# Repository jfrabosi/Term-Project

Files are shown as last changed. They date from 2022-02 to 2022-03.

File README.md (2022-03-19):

# Project Proposal
The project our team is planning on developing is a pancake plotter. This system uses a 2.5 axis CNC system to interpret code and plot the batter on a griddle. 
The batter is contained in a 500 mL syringe which is moved along a radial arm via a motor belt system. The raidial arm is mounted to a second motor
which can rotate from -90 to 90 degrees. To reduce the amount of stress on the second motor, a semi-circle will be used to support the end of the radial 
arm. We plan to fabricate the entire system by using 80/20 1" tubing as the structure, using a gridle as a bed, using 3D-printed parts as mounts, and
using laser-cut plywood for the semi-circular support. A bill of materials, breaking down cost, as well as sketches and a gif of our system design can be seen in the figures below.

| Qty. | Part | Source | Est. Cost |
|:----:|:---|:---|:---:|
|  3 | Pittperson Gearmotors | ME405 Tub | - |
|  1 | Nucleo with Shoe | ME405 Tub | - |
|  1 | 500 mL Syringe | Amazon | $15.99  |
|  1 | Griddle | Amazon | $26.94  |
|  3 | 80/20 1" Tubing | Amazon | $14.54  |
|  1 | Spool PLA Plastic | Team's Supply | - |
|  1 | Sheet of Plywood | Amazon | $24.00  |
|  3 | Motor Driver | ME 405 Tub and Pololu | $4.95 |

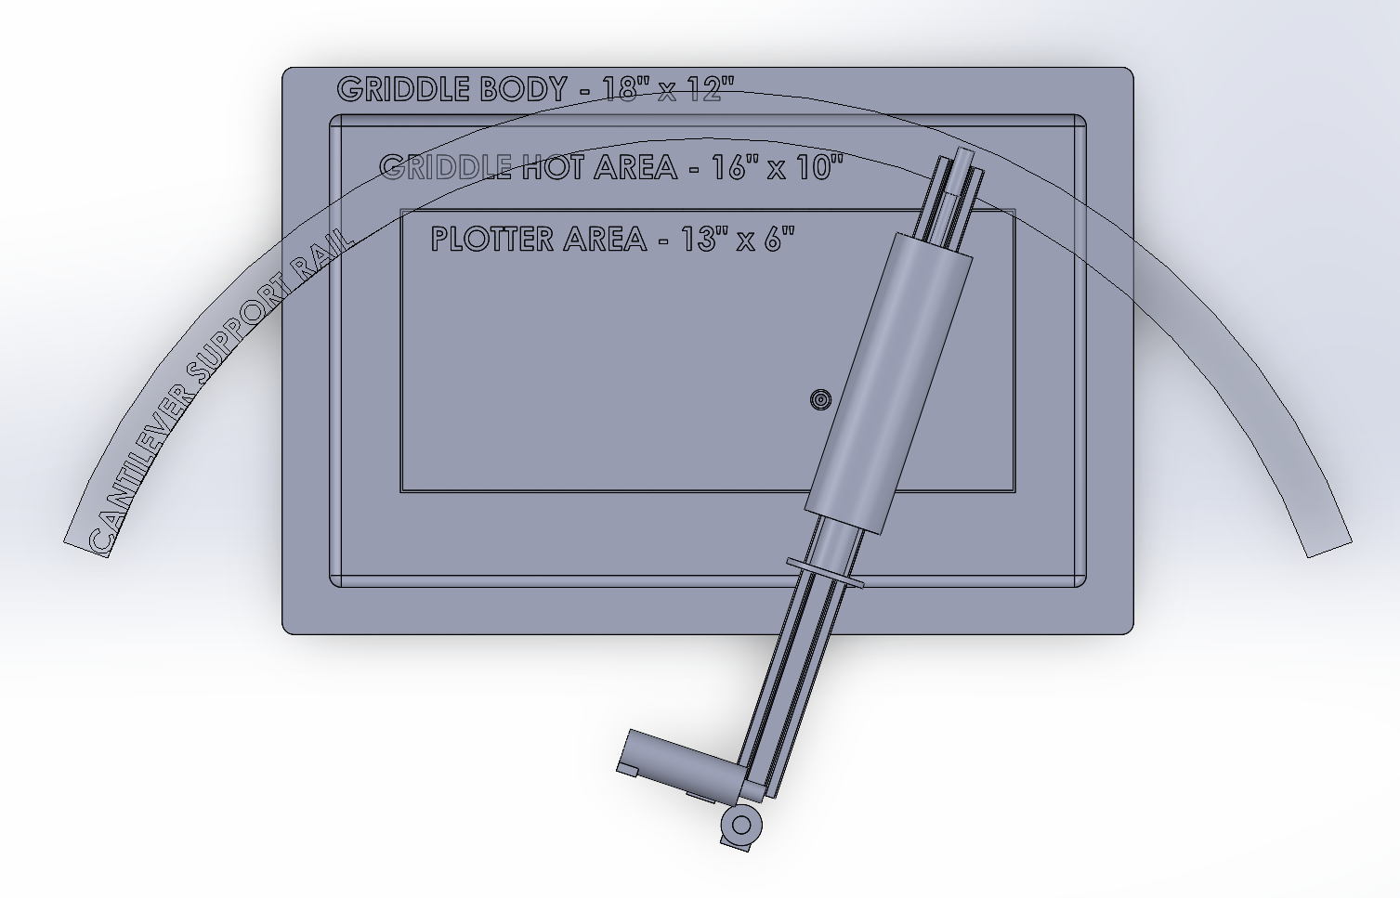
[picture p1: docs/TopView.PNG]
top down view


FIGURE 1. Top-down view of our overall system.

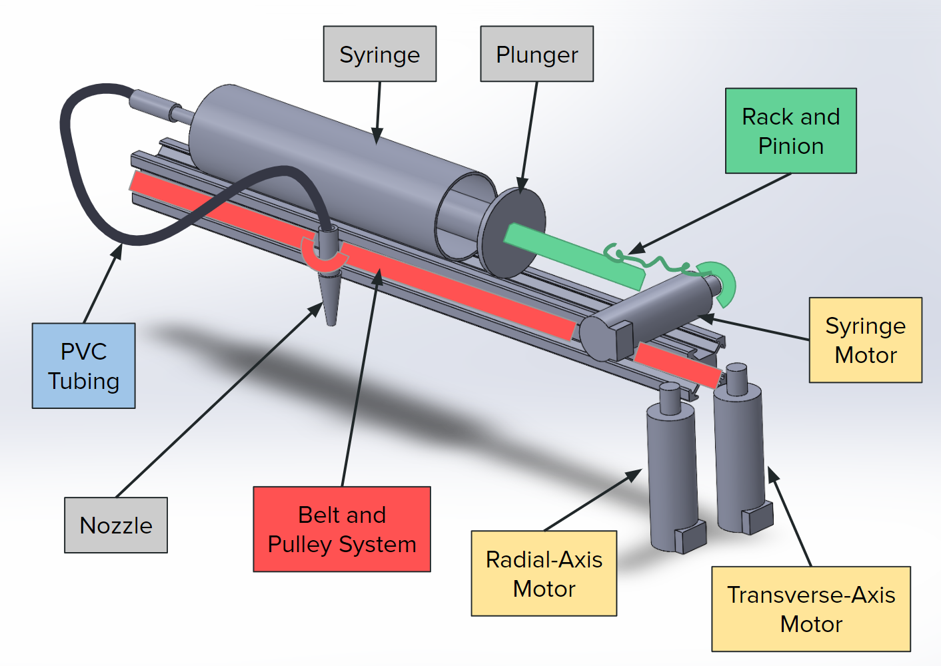
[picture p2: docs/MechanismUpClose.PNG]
close-up


Figure 2. Close-up view of our extruder mechanism.

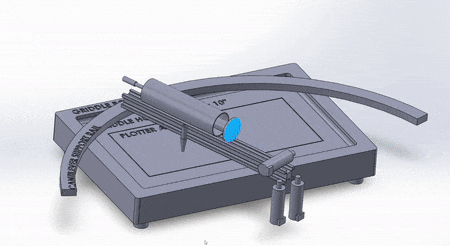
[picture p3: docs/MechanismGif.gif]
gif of the assembly


Figure 3. Gif of our CAD assembly moving

real assembly with pen

Figure 4. Gif of our physical assembly plotting a rectangle with a pen attached

real assembly with batter

Figure 5. Gif of our physical assembly strategically disassembling itself

# HARDWARE DESIGN
This section describes the mechanisms, mechanical design, and
manufacturing techniques for each component of our 2.5D plotter.
Each subsection below describes a different component of the design,
explaining how and why we made the decisions that we did.
                
## GENERAL IDEA
Our interpretation of a 2.5D plotter is a pancake plotter: a mechanism
that can convert G-Code of an image to carefully-positioned pancake
batter deposited onto a hot griddle, ideally making a pancake in the
shape of the chosen image.

Our team plans to accomplish this using three axes of motion: one
rotational, one transverse, and one
also-transverse-but-it's-for-dispensing-batter. The finished mechanism
almost resembles a windshield wiper with a nozzle that moves along the
length of the blade, allowing us to cover a wide area with two motors.
A third motor will dispense the batter using a lead screw for precise
depositing. A GIF of the mechanism can be seen above in Figure 3.

It should be noted that the rotational-transverse design
is a challenge: surely a Cartesian (X-Y) plotter would be simpler. But
hey, we're Cal Poly MEs; we can take the challenge.

A Bill of Materials (BOM) can be found at the end of this section, listing
names, suppliers, quantities, and costs for each purchased or designed item.

Additionally, all CAD files can be found in the /docs/SOLIDWORKS directory
of this repository.

## GRIDDLE
This is the most straight-forward component. In order to make pancakes,
you need a griddle or other hot-implement. Our team chose the griddle below,
purchased from Amazon for $27, due to its reasonable price and fast shipping
time (did I mention this project only took four weeks?).

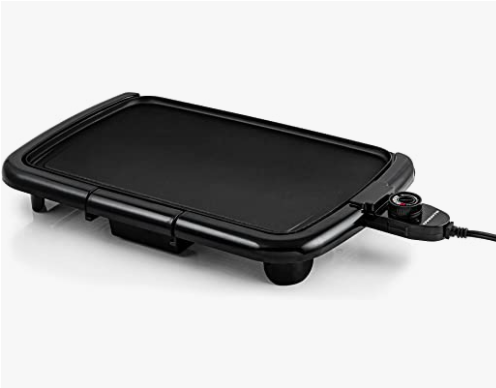
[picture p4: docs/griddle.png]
griddle


Figure 6. The griddle

There's really not much else for this one. It's a griddle.

## SUPPORT STRUCTURE
In order to effectively position and control our motors, our design first
needed a support structure. We designed the base of the support structure
from aluminum extrusions due to their versatility (used for both the
supports and the actuating rail!), low cost, and fast shipping. Our team
purchased L-shaped brackets that fit within the extrusion rails for securing
multiple components to the support structure - these brackets were used in
almost every component of the design. We were able to laser-cut a piece
of plywood to create our support rail that the mechanism rests and slides
on in our on-campus machine shops. Lastly, we designed and 3D-printed some
inserts / risers that elevated the support rail above the griddle. The risers
were printed in PLA and are positioned far enough from the heating element
to reduce the risk of heat deformation.

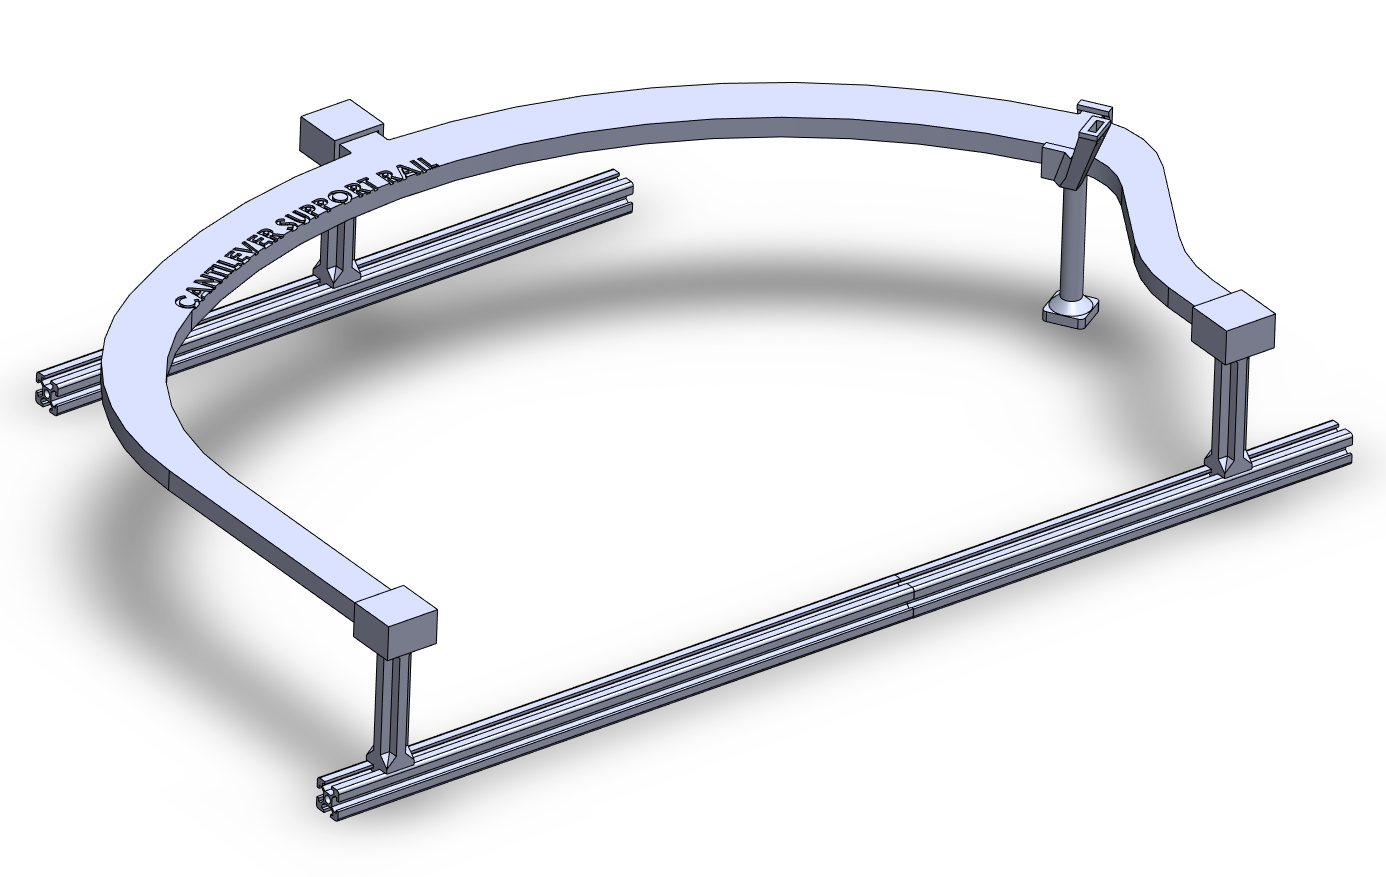
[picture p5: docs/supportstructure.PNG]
support structure


Figure 7. The support structure

Purchasing aluminum extrusions and L-brackets, laser-cutting the plywood
on-campus, and 3D-printing the risers allowed us to keep costs low,
reduced our manufacturing time (as opposed to machining metal), and
allowed for rapid prototyping and design changes (of which there were many)!

## BATTER DISPENSER
Time for moving parts!

This component is the "0.5" axis of our 2.5 axis plotter. It dispenses batter
at a constant rate when told to by the microcontroller, and is made up of a
syringe for holding batter, an endstop for securing the syringe, a plunger
mechanism for pushing the batter, a motor and lead screw for creating linear
dispensing motion, and a PVC tube for moving batter to the nozzle holder.

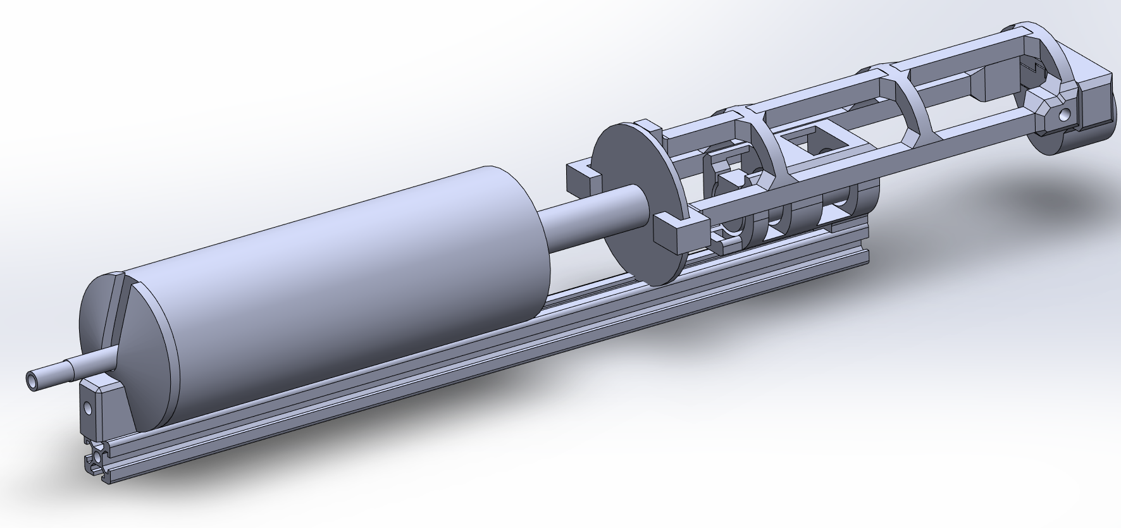
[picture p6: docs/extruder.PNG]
extruder


Figure 8. The extruder mechanism

## TRANSVERSE MOTION
To move the location at which batter dispenses (essentially, the location of the
nozzle), we used two axes of motion: transverse (parallel to the syringe) and
radial (rotational about a center axis).

For the transverse motion, we used a belt-driven mechanism that began at our nozzle
carrier. The nozzle carrier has two rectangular slots for the two ends of the belt
to slot into, then two L-brackets slip into the same slots and can be tightened
to fix the belts in position and tension our entire belt system.

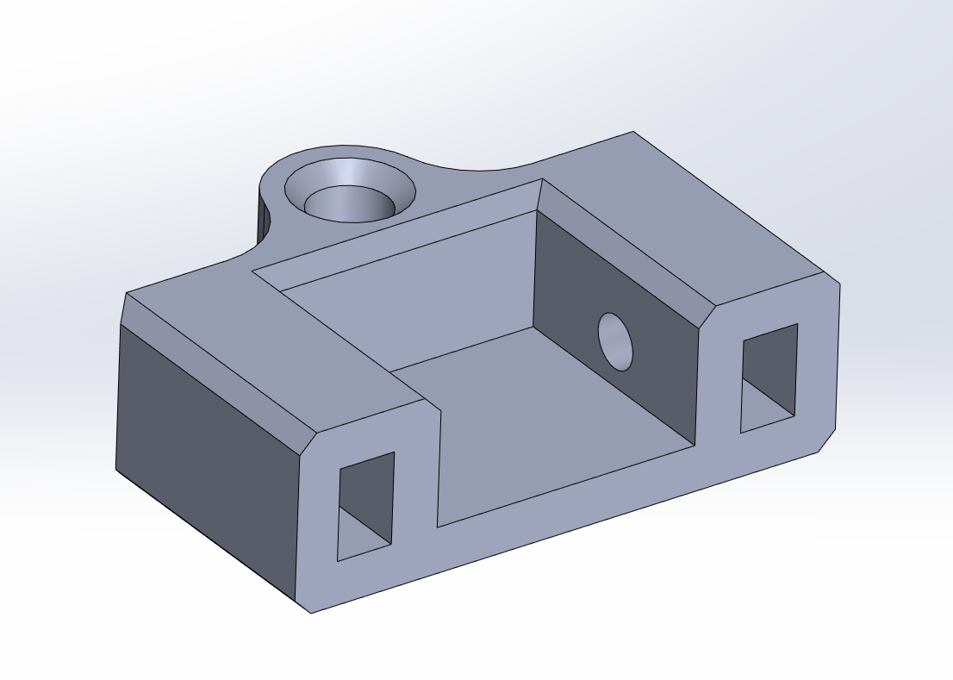
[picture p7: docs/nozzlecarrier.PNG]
nozzle carrier


Figure 9. The nozzle carrier

At either end of the aluminum extrusion there are two 3D-printed parts that slot
into the extrusion ends using careful geometry. The far end piece has three uses:
one, it is used as a pulley for the transverse motion belt; two, it is used as a
load-bearing wheel to ride along the wooden support rail; and three, it holds a limit
switch for the transverse axis. 

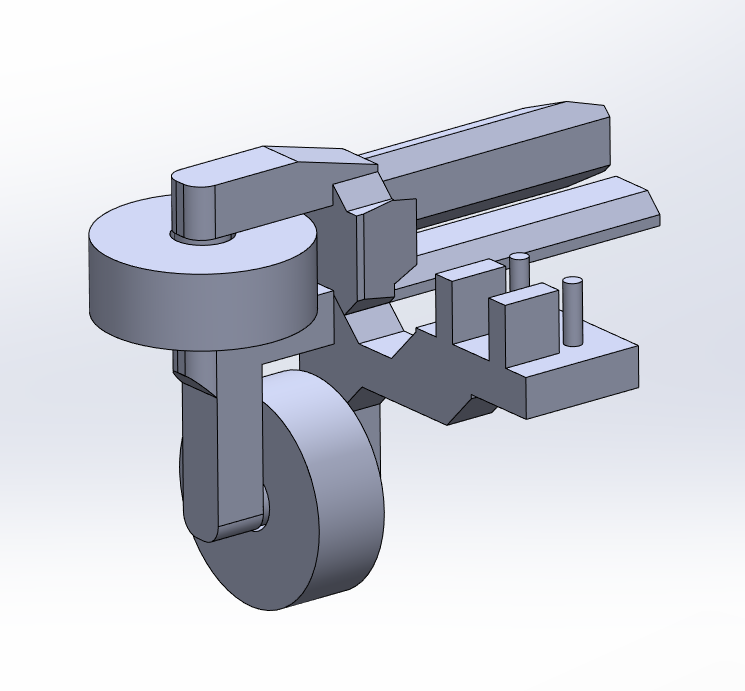
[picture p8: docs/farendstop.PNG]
far end stop


Figure 10. The far end stopper

The other end stop also has multiple uses: one, it holds the transverse axis motor
which drives the belt mechanism; and two, it interfaces with the power transmission
block for the rotational motion motor.

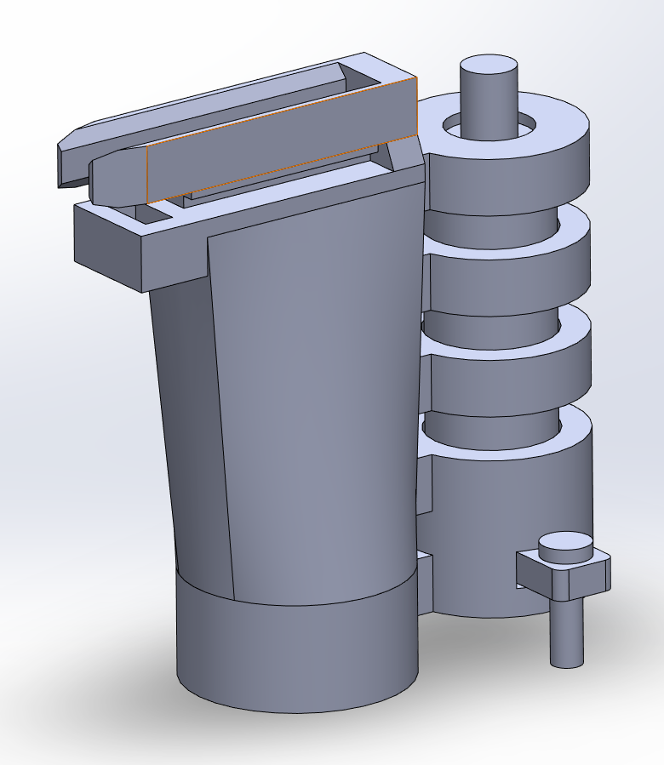
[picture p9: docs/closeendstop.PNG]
close end stop


Figure 11. The close end stopper

The belt then slides between the slots in the aluminum extrusion. In practice, we
found that this design produced a lot of friction within the transverse axis and
our motor had difficulties providing enough torque to move the nozzle carrier
reliably.

## ROTATIONAL MOTION
For the rotational axis of motion, we used a power transmission block that was
3D-printed (using resin/SLA printing as opposed to the "normal" plastic/FDM 
printing used elsewhere in the project). We used resin printing due to the tight
tolerance requirements associated with this axis of motion; a small bit of backlash
at the rotational motor would amplify over the nearly 14" aluminum extrusion. This
block slotted onto the D-shaft of our high-torque rotational axis motor, and the
edges of the cube then slotted into a tight-fitting cavity on the close end stopper
in the previous section.

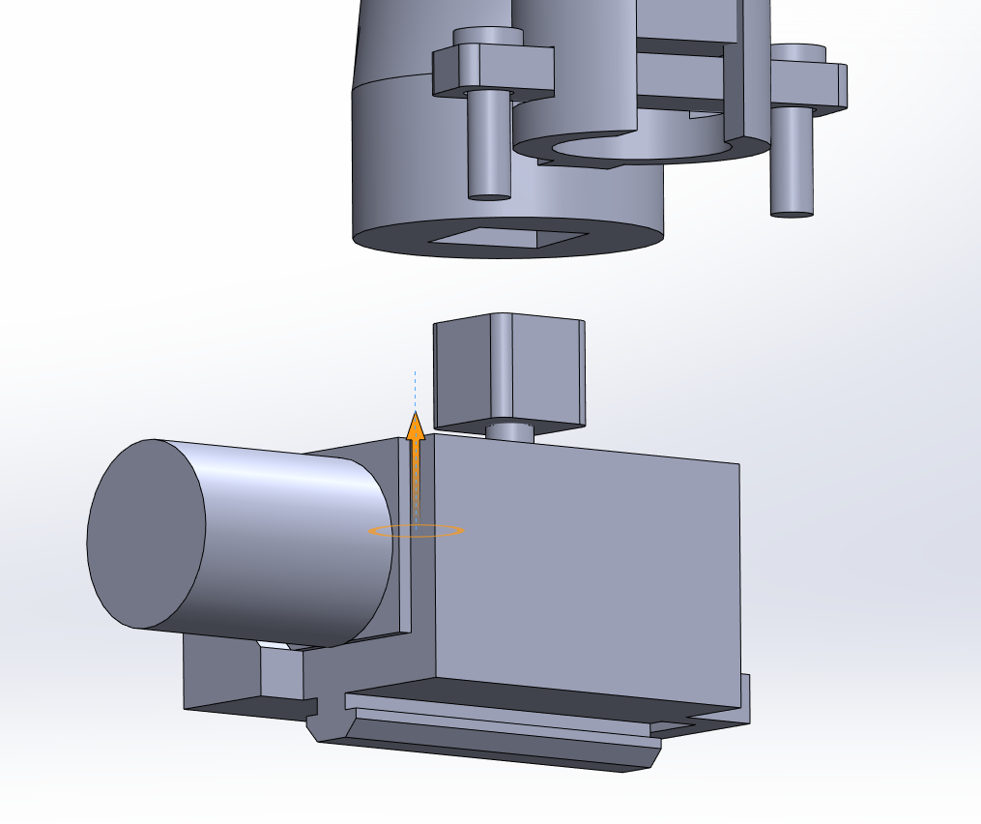
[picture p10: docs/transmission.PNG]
transmission system


Figure 12. The rotational power transmission system

The DC motor then slotted into a 3D-printed housing that interfaced with an
aluminum extrusion part of the support system. This component was ultimately our
worst-performing component: after lots of testing, the power transmission cube
and housing began to show severe signs of wear and produced very large amounts of
backlash into our system.

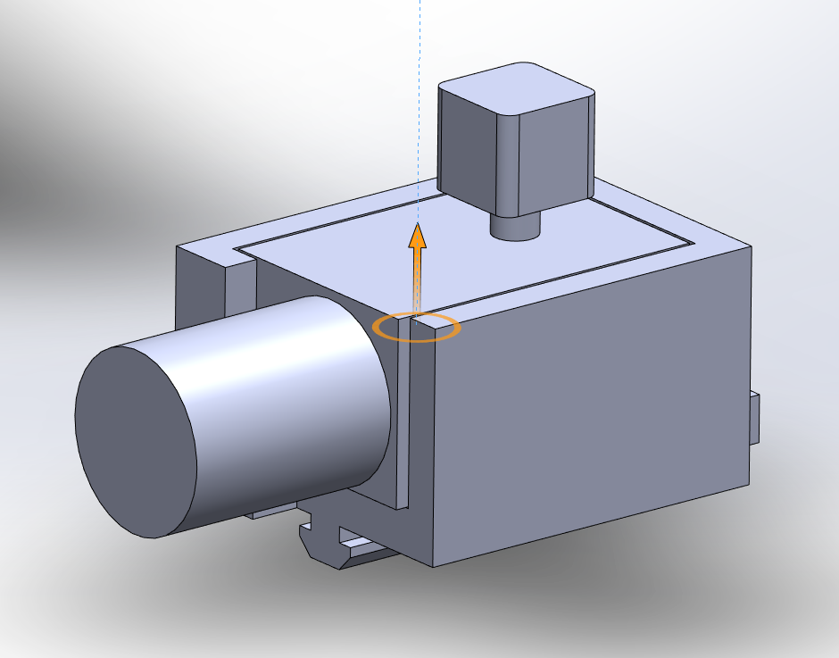
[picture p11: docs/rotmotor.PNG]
rotational motor housing


Figure 13. The rotational motor and housing

## LIMIT SWITCHES AND "ZEROING"
To figure out where all of our motors were at the beginning of each "print", we
devised a system using limit switches to trigger when each axis was at its "zero"
position. For the transverse axis, we positioned the limit switch at the far end
of the aluminum extrusion as part of the far end stopper part. For the rotational
axis, we positioned the limit switch at the furthest-right position on the wooden
support rail, as part of a 3D-printed weight supporter.

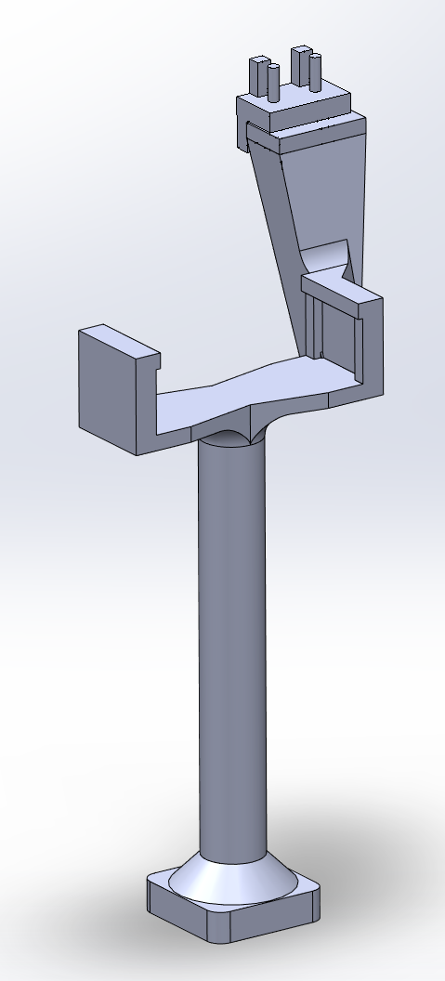
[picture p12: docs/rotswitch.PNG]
rotational limit switch


Figure 14. The rotational limit switch

We created a unified limit-switch holder based on the geometry of the limit switches
we purchased (listed in the BOM). The geometry is very precise and thus required
all of the limit switch holders to be 3D-printed in resin. For the transverse axis,
the entire end stopper was printed in resin so this wasn't an issue. However, for
the rotational axis, you can see a small part sitting atop the larger structure.
The large structure is FDM, while the small part is resin.

For the batter extrusion axis, we took a slightly different approach. Instead of
zeroing this axis at the start of each print, we positioned a limit switch between
the plunger and the syringe housing so it would be activated when the plunger was
fully closed (and therefore there was no more batter to dispense). This part was
resin printed and used an L-bracket to attach to the rail.

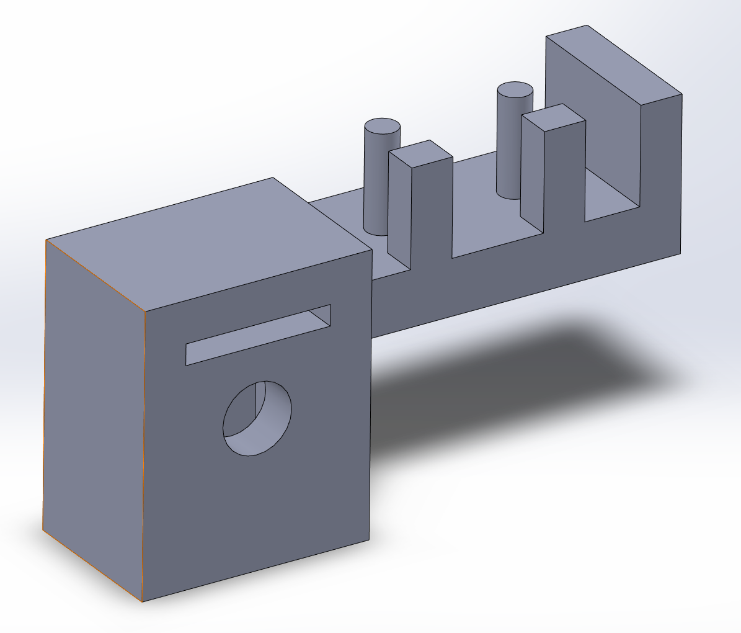
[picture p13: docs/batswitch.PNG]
batter limit switch


Figure 15. The batter extrusion limit switch

## SOFTWARE ADDENDUM

Our task diagram and two motor FSMs (radial and transverse) can be seen below.

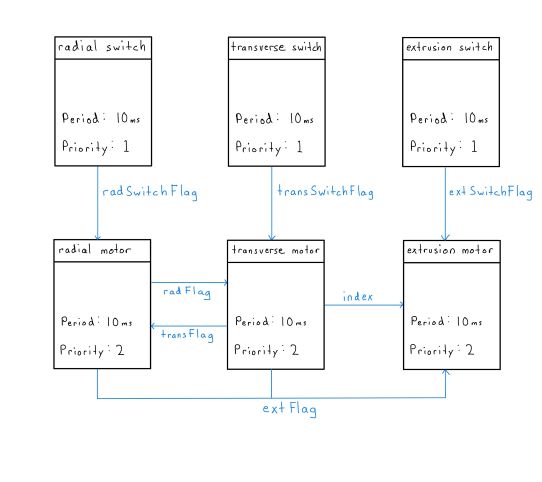
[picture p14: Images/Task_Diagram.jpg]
task diagram


Figure 16. Task diagram 

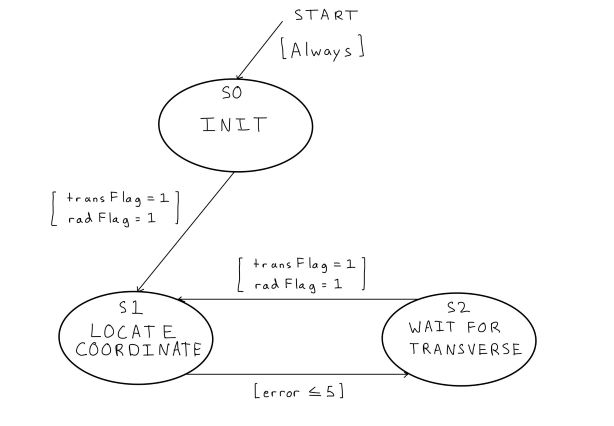
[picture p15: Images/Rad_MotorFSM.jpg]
rad FSM


Figure 17. Radial motor FSM

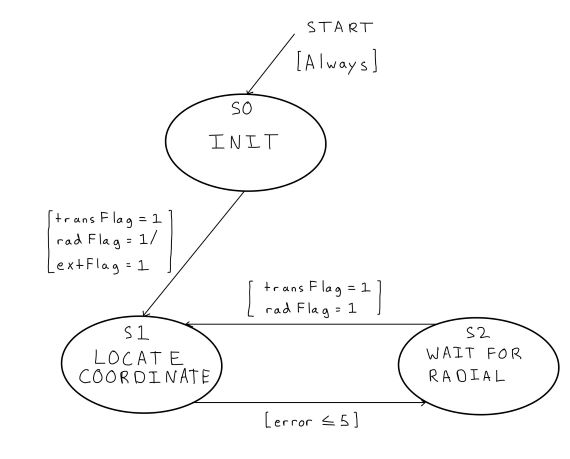
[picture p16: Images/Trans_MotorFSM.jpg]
trans FSM


Figure 18. Transverse motor FSM

## RESULTS
After assembling the pancake plotter and uploading the code to the Nucleo STM 32,
our group was able to successfully plot a square using a marker and g-code created 
by taking points on an image and converting them to polar corrdinates using a cartesian 
to polar converting script. When implementing the pancake batter and syringe into the 
system, the team ran into issues with the amount of torque transmitted by the radial 
axis motor. The torque required to accurately recreate the square pattern we had achieved 
with the marker required a much higher torque than our motor and fixture could apply.
The pancake  batter and syringe added too much weight on the cantilever beam which after 
much testing resulted in our mechanism transferring power from the motor to the shaft 
shattering. Despite not being able to implement the pancake batter, the team found 
success in being able to plot a shape given the cartesian coordinates with a reasonable 
degree of accuracy, proving that our concept worked through the use of our designed 
hardware and corresponding code.

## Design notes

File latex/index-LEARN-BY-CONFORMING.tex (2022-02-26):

\hypertarget{index_sec_1}{}\doxysection{SOFTWARE DESIGN}\label{index_sec_1}
This section will cover the tasks that we plan on utilizing for our 2.\+5 axis machine. The main taks that we will need include a G-\/\+Code task thatconverts G-\/code into usable coordinates, a radial motor task, a transverse motor task, and a syringe motor task. The task diagram below shows how we plan on implimenting these tasks into our design through the use of queue and share objects. each task will be discussed more i depth in the following sections.\hypertarget{index_autotoc_md0}{}\doxysubsection{Include picture of task diagram}\label{index_autotoc_md0}
\hypertarget{index_G-CODE}{}\doxysubsection{TASK}\label{index_G-CODE}
The G-\/\+Code task will be responsible for the conversion a G-\/\+Code into coordinates that can be used by our machine. This will be accomplished by first converting the G-\/\+Code file into cartesian coordinates through the use of splicing and appending. These will then be converted to polar coordinates using conversion formulas. The radial and transverese coordinates will then be split into seperate quees and then sent off to the appropiaate motor task.\hypertarget{index_autotoc_md1}{}\doxysubsection{FSM?}\label{index_autotoc_md1}
\hypertarget{index_RADIAL}{}\doxysubsection{MOTOR TASK}\label{index_RADIAL}
The radial motor task will be responsible for the radial motion of our nozzle. This task will function by taking the radial coordinates from the G-\/\+Code task and using these values as refernece point for a controller object. The output of the controller will then be used to apply a duty cycle to the radial motor. Since we will be utilizing the encoder to measure position, it will be important to convert the rotational motion of the encoder to a linear distance that we can compare the radial coordinates against. Once the desired coordinate is reached, a flag variable will be sent out to the syringe motor task indicating it is ready for pancake mix to be dispersed.\hypertarget{index_autotoc_md2}{}\doxysubsection{FSM?}\label{index_autotoc_md2}
\hypertarget{index_TRANSVERSE}{}\doxysubsection{MOTOR TASK}\label{index_TRANSVERSE}
The transverse motor task will be responsible for the transverse motion of our nozzle. This task will function by taking the transverse coorinates coordinates from the G-\/\+Code task and using these values as reference points for a controller object. The output of the controller object will then be used to apply a duty cycle toi the transverse motor. Since we will be using the encoders to measure position, we need to make sure that the encoder reads degrees and not ticks. Once the desired coordinate is reached, a flag variable will be sent out to the syringe motor task indicating it is ready for pancake mix to be dispersed.\hypertarget{index_autotoc_md3}{}\doxysubsection{FSM?}\label{index_autotoc_md3}
\hypertarget{index_SYRINGE}{}\doxysubsection{MOTOR TASK}\label{index_SYRINGE}
The syringe motor task will be responsible for the dispersion of the pancake mixture.

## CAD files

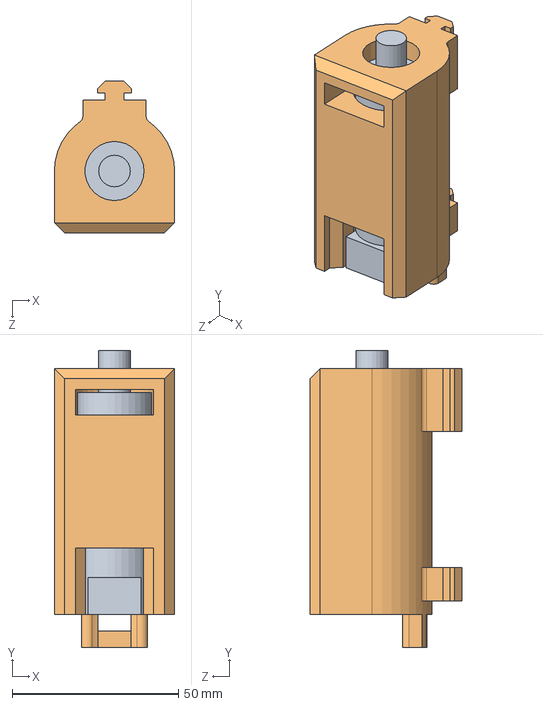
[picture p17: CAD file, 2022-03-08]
docs/SOLIDWORKS/leadAssem.SLDASM
36.2 x 89.4 x 45.6 mm
Motor
leadMotorHousing^leadAssem

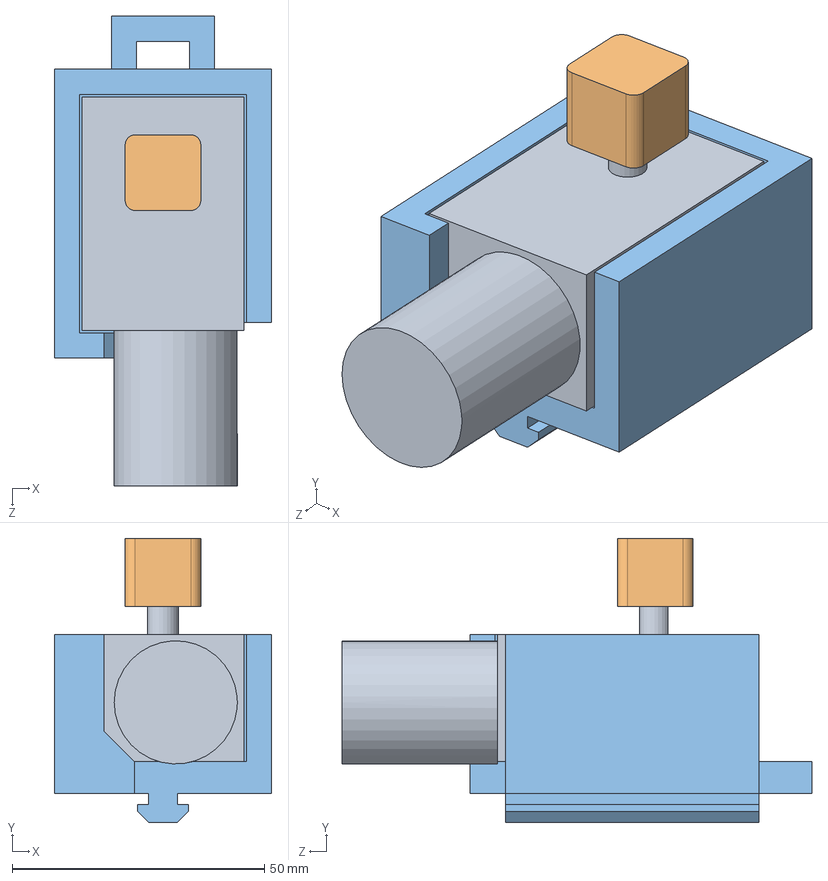
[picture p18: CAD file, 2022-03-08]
docs/SOLIDWORKS/thetaAssem.SLDASM
43.0 x 56.3 x 93.0 mm
radialMotor
radialPlug^thetaAssem
thetaHousing

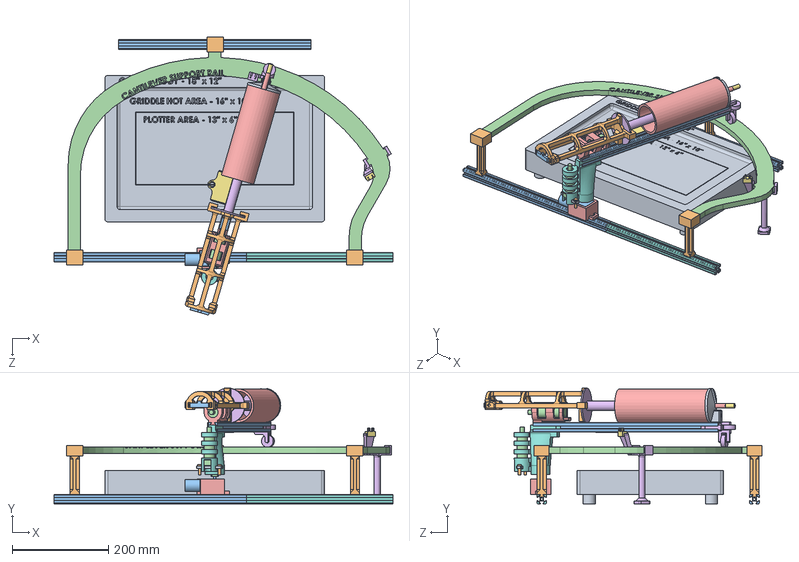
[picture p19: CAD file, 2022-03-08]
docs/SOLIDWORKS/PrelimAssembly.SLDASM
704.8 x 240.6 x 578.5 mm
Griddle
railGrabber x 3
14L1W8020 x 3
cantileverSupportRailV2
Syringe
Plunger
PVCstub
14L1W8020shorter
endStop
pusher
Part8^pusherAssem
Motor x 2
leadMotorHousing^leadAssem
endRoller
nozzleHolder^nozzleAssem
radialGearAttach
Part13^radialGearAssem
Part14^radialGearAssem x 2
radialMotor
radialPlug^thetaAssem
thetaHousing
railSupport
limitPlug

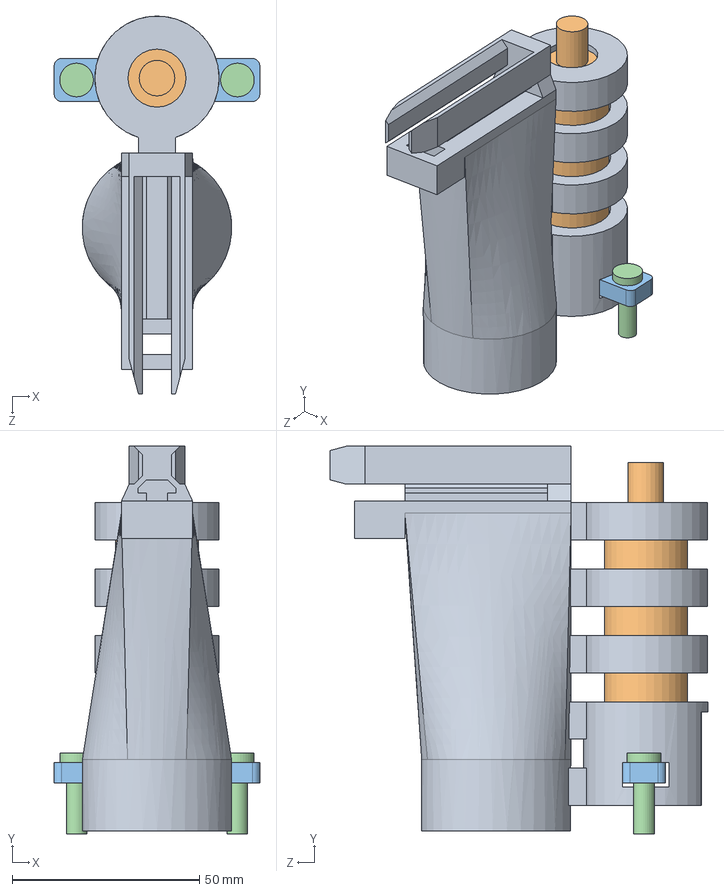
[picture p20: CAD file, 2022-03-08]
docs/SOLIDWORKS/radialGearAssem.SLDASM
55.0 x 103.6 x 101.1 mm
radialGearAttach
Motor
Part13^radialGearAssem
Part14^radialGearAssem x 2

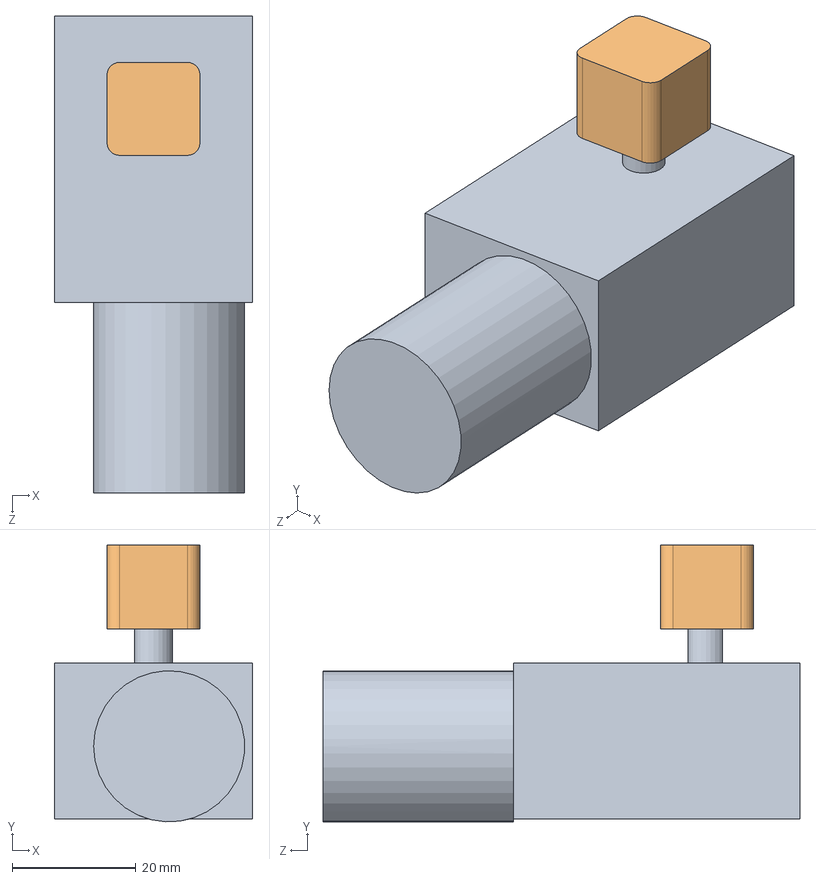
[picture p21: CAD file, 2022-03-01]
docs/SOLIDWORKS/radialAssem.SLDASM
32.0 x 44.7 x 77.0 mm
radialMotor
radialPlug^radialAssem

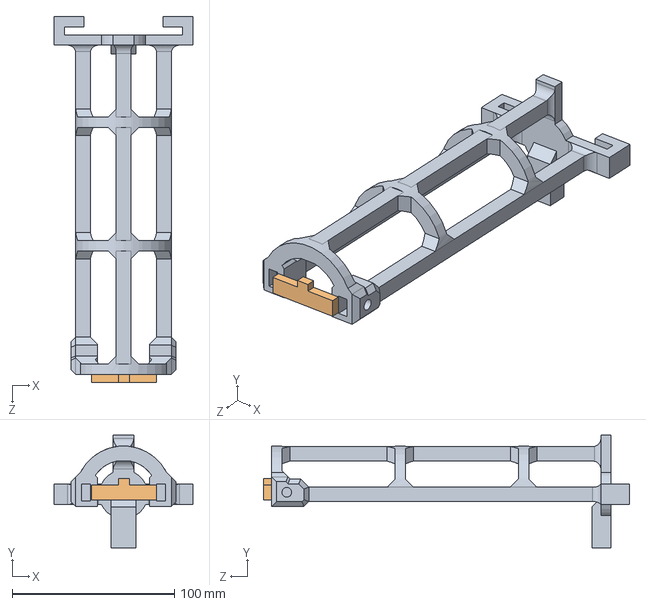
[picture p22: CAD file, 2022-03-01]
docs/SOLIDWORKS/pusherAssem.SLDASM
85.7 x 69.5 x 225.9 mm
pusher
Part8^pusherAssem

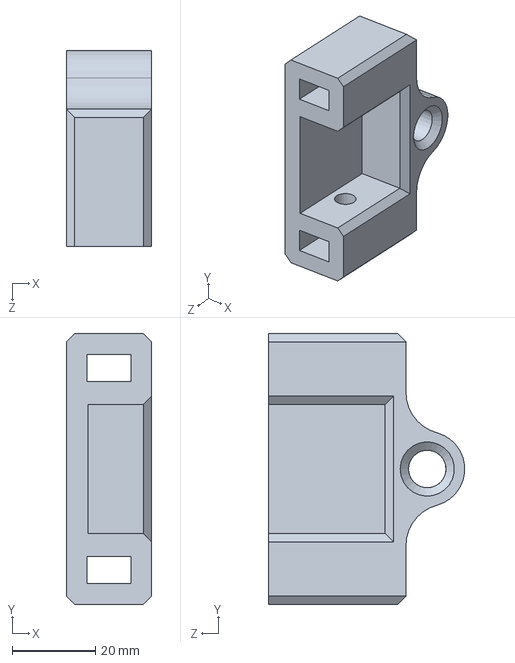
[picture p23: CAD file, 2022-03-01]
docs/SOLIDWORKS/nozzleAssem.SLDASM
20.5 x 65.0 x 47.1 mm

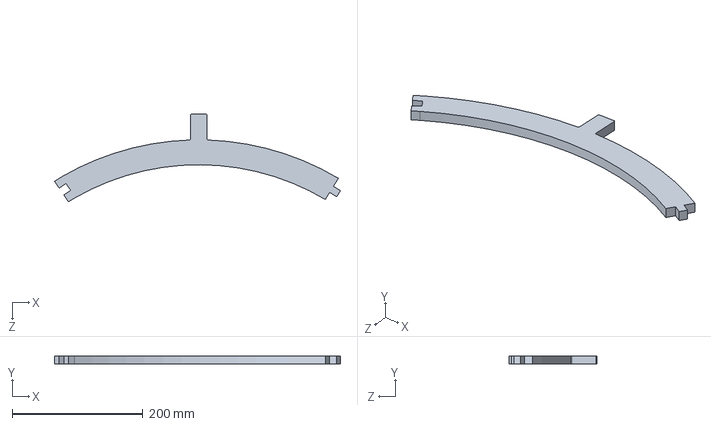
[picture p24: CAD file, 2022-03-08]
docs/SOLIDWORKS/cantileverSupportRailV2.SLDPRT
438.0 x 12.7 x 134.3 mm

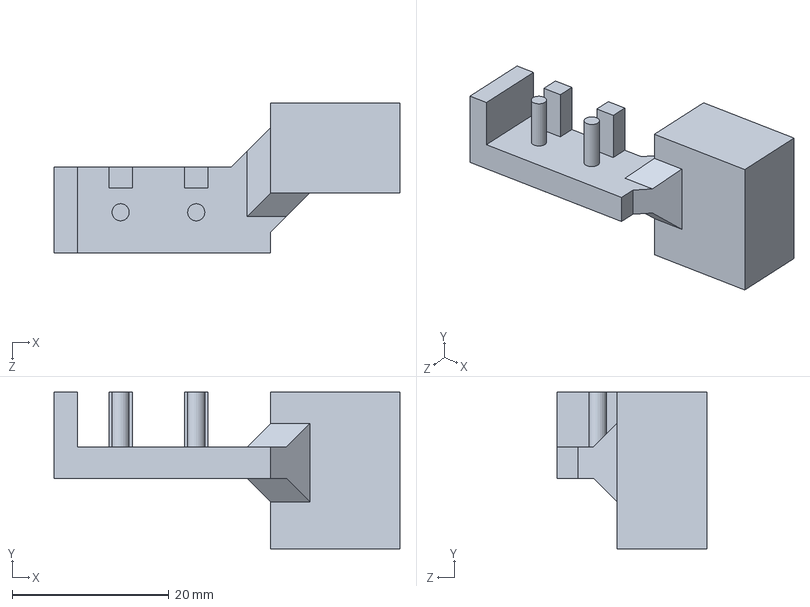
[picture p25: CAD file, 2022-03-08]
docs/SOLIDWORKS/limitRider.SLDPRT
44.2 x 20.0 x 19.2 mm

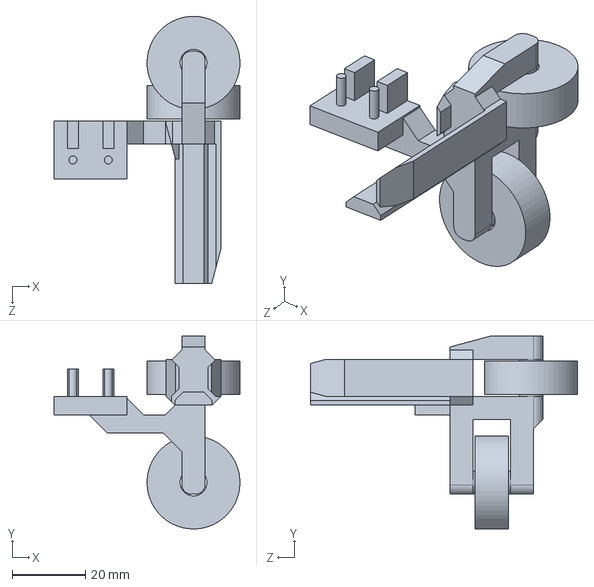
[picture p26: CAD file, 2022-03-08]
docs/SOLIDWORKS/endRoller.SLDPRT
50.8 x 52.7 x 73.0 mm

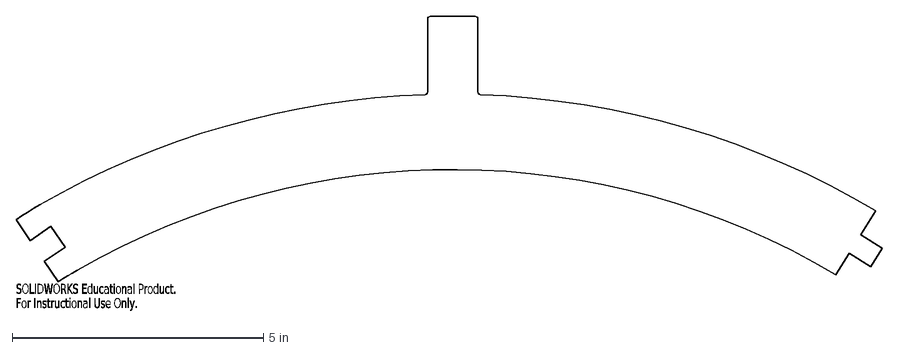
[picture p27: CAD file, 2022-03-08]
docs/SOLIDWORKS/rail3.DXF
SOLIDWORKS Educational Product.
For Instructional Use Only.

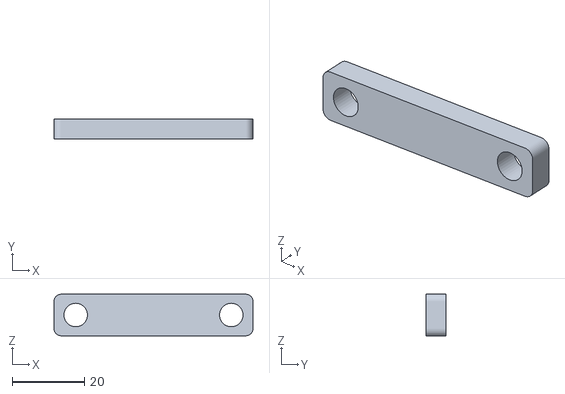
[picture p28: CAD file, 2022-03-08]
docs/SOLIDWORKS/Part13^radialGearAssem.STL
55.0 x 5.50 x 11.5

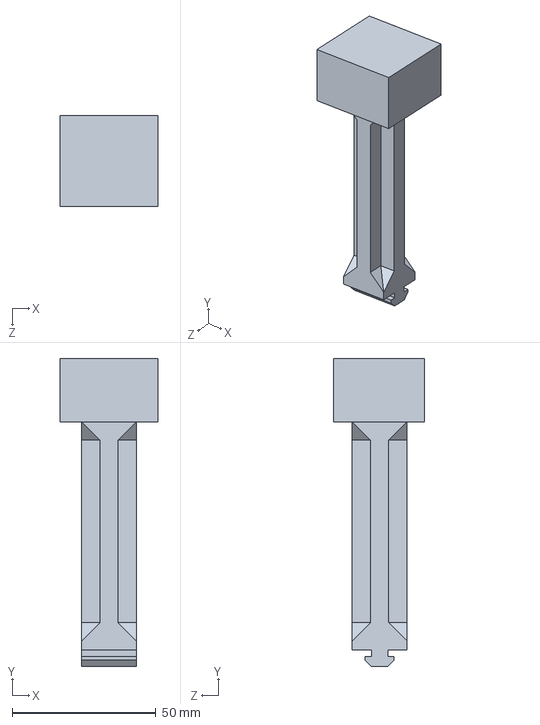
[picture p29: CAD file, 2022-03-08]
docs/SOLIDWORKS/railGrabber.SLDPRT
34.0 x 107.1 x 31.8 mm

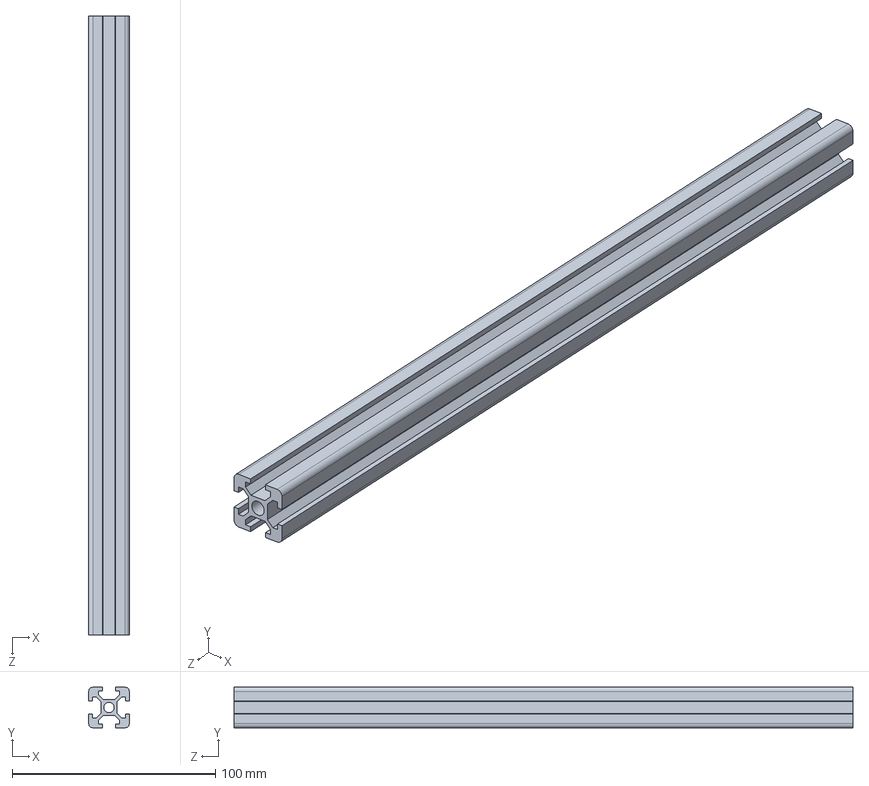
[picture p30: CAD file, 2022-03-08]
docs/SOLIDWORKS/14L1W8020shorter.SLDPRT
20.0 x 20.0 x 304.8 mm

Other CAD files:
docs/SOLIDWORKS/radialGearAttach.SLDPRT
docs/SOLIDWORKS/rail1.DXF
docs/SOLIDWORKS/leadMotorHousing^leadAssem.STL
docs/SOLIDWORKS/Part14^radialGearAssem.STL
docs/SOLIDWORKS/14L1W8020.SLDPRT
docs/SOLIDWORKS/Griddle.SLDPRT
docs/SOLIDWORKS/Motor.SLDPRT
docs/SOLIDWORKS/Nozzle.SLDPRT
docs/SOLIDWORKS/PVCstub.SLDPRT
docs/SOLIDWORKS/Plunger.SLDPRT
docs/SOLIDWORKS/SlideRail.SLDPRT
docs/SOLIDWORKS/Syringe.SLDPRT
docs/SOLIDWORKS/endRoller.STL
docs/SOLIDWORKS/endStop.SLDPRT
docs/SOLIDWORKS/endStop.STL
docs/SOLIDWORKS/leadScrewMount.SLDPRT
docs/SOLIDWORKS/limitPlug.SLDPRT
docs/SOLIDWORKS/limitPlug.STL
docs/SOLIDWORKS/limitRider.STL
docs/SOLIDWORKS/nozzleAssem.STL
docs/SOLIDWORKS/pusher.SLDPRT
docs/SOLIDWORKS/pusher.STL
docs/SOLIDWORKS/pusherAssem - Part8^pusherAssem-1.STL
docs/SOLIDWORKS/pusherAssem - mounter^pusherAssem-1.STL
docs/SOLIDWORKS/pusherAssem - pusher-1.STL
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

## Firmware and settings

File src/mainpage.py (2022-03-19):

'''!
@file                mainpage.py
@brief               Brief doc for mainpage.py
@details             Detailed doc for mainpage.py 


@mainpage

@section sec_1  SOFTWARE OVERVIEW
                This section will cover the various drivers used in our system
                as well as what tasks they were utilized in. The tasks themselves
                be discussed in a later section.
@subsection 1s1                
                ##MOTOR DRIVER
                The motor driver script contains class files that allow us to
                apply pwm to our dc motors. Since we are utilizing two diffrent
                motor shield we have two separte class files since each motor
                shield utilizes a diffrent amount of pins. The motor driver is
                utilized in all of outr motor tasks in order to apply a duty
                cycle.
                
@subsection 1s2
                ##ENCODER DRIVER
                The encoder driver script contains a class file that allows us
                perform various functions with the encoders on the motors. These
                functions enclude reading the position of the encoder, zeroing
                the position of the encoder and overwriting the position of 
                the encoder wit ha custom value. The encoder driver is used in all
                of our motor tasks in order to locate read out our transverse
                and radial positions.
@subsection 1s3
                ##CONTROLLER
                The controller script contains a class file that allows us to 
                perform PID control. It contains functions for setting our gain
                values and setpoints. It also contains a function to compute the 
                total error in our system. This file is used by our motor tasks
                in order to impliment positional control.
@subsection 1s4
                ##LIMIT SWITCH
                The limit switch script is a short script that contains a class
                file that allows us to check the status of our limit switches.
                It contains a function that will return the pin value when called.
                This file is used in our limit switch tasks in order to update key
                flag variables depending on whether or not the limit switches 
                are actuated.
@subsection 1s5
                ##G-CODE
                The gcode_convert script is a function file that contains a 
                function that takes a .nc file, converts it to three seperate
                lists containing cartesian coordinates, and then conversts those
                lists to cartesian coordinates. This file is used in our execution
                script in order to create the lists that will be used by our
                various motor tasks.
                
@subsection 1s6
                ##TASK_SHARE & COTASK
                The task_share and cotask scripts were scrips that were shared with
                us in lecture in order to imoliment cooperative multitasking.
                The task_share file allows us to create shared variables to be used
                among our generators while the cotask file allows us to turn our 
                generators into tasks and run them simultaneously.
                
@section sec_2  TASK STRUCTURE
                This section will cover the tasks that we plan on utilizing for
                our 2.5 axis machine. The main taks that we will need include 
                a G-Code task thatconverts G-code into usable coordinates, a
                radial motor task, a transverse motor task, and a syringe motor 
                task. The task diagram below shows how we plan on implimenting
                these tasks into our design through the use of share 
                objects. each task will be discussed more in depth in the following 
                sections.
                
                ![task diagram](https://github.com/jfrabosi/Term-Project/blob/main/Images/Task_Diagram.jpg)
                
@subsection 2s1
                ##RADIAL LIMIT SWITCH TASK
                The radial limit switch task continuouslly checks to see if the 
                limit switch for the radial motor has been actuated. This is 
                accomplished through the use of a shared flag variable. When the
                task is initialized the value of this shared variable is set to 
                zero. When the limit switch is finally actuated, the value of 
                the shared variable is changed to one, this is then used to start
                the plotting portion for the radial motor task.
                
@subsection 2s2
                ##TRANSVERSE LIMIT SWITCH TASK
                The transverse limit switch task continuouslly checks to see if the 
                limit switch for the transverse motor has been actuated. This is 
                accomplished through the use of a shared flag variable. When the
                task is initialized the value of this shared variable is set to 
                zero. When the limit switch is finally actuated, the value of 
                the shared variable is changed to one, this is then used to start
                the plotting portion for the transverse motor task.
@subsection 2s3
                ##EXTRUSION LIMIT SWITCH TASK
                The extrusion limit switch task continuously checks to see if the 
                limit switch for the extrusion motor task has benn actuated.
                
@subsection 2s4 
                ##RADIAL MOTOR TASK
                The radial motor task will be responsible for the radial motion
                of our nozzle. In order to accomplish this the radial motion will
                first locate itself using the limit switch located on its path.
                When the task first runs the radial motor will move the arm 
                slightly away from, and then towards the limit switch until it
                makes contact with it. Once the arm makes contact with the limit
                switch, the position of the encoder is updated to correspond
                with the the position of the limit switch. It will also wait 
                for the transverese motor to make contact with its limit switch 
                before proceeding. This will all be done in the initialization
                state S0 shown in the FSM below. Once contact with the radial
                and transverse limit switches has been made, the flag variables for
                each of those motors will be changed to one, and thus the
                task will transition into the next state S1, which is locating the
                radial coordinates. In this state, the task will make its way
                through a provided list of coordinates using a PI controller for
                positional control in order to get as colse to the desired value
                as it can. A constant duty cycle will be applied to the motor
                as it moves from index to index. In case the radial motor reaches
                its desired index value before the transverse motor, it will enter 
                an idler state, S2, where it will wait for the trnasverse motor 
                to reach its index value before continuing. This state also uses
                the aforementioned flag variables to make sure that each motor has
                reached its appropriate index value.
                
                ![rad FSM](https://github.com/jfrabosi/Term-Project/blob/main/Images/Rad_MotorFSM.jpg)
                
@subsection 2s5
                ##TRANSVERSE MOTOR TASK
                The transverse motor task will be responsible for the transverse
                motion of our nozzle, and is very similar in functionality to the
                radial motor task. The task begins by locating itself in the 
                initialization state S0 in the same manner as the radial motor task,
                the only difference being that this task is also responsible for
                updating the flag variable for the extrusion task so that it can begin 
                its cycle. After the task has gone through the initialization state, it 
                moves onto S1, locating coordinates. In the same manner as the radial
                motor task, this tak also has its own list that it iterates through
                using positional control to get as close to the desired values as it
                possibly can. This task also contains an idler state in case it reaches its
                index value before the radial motor task. Once both tasks reach their index
                value the flag variables are updated and they move onto the next value
                in their respective lists.

                ![trans FSM](https://github.com/jfrabosi/Term-Project/blob/main/Images/Trans_MotorFSM.jpg)
                
@subsection 2s6
                ##EXTRUSION MOTOR TASK
                The extrusion motor task will be responsible for the actuation of
                syringe that will dispense our pancake batter onto the plotting
                surface. The task stats by first moving the motor to make sure that
                no pressure is being applied on the syringe. Once this is done, the
                task begins going through its list of actuation values. This list 
                simply contains 0's and 1's, a one indicating to extrude batter. In order
                to make sure that batter is only extruded once the radial and transverse
                motor tasks have rached their proper locations, a shared index variable
                is used. This variable is sent to the extrusion task after both the
                radial and transverse motor tasks have reached their location, and it 
                ensures that all three tasks are operating on the same index, and thus
                batter is only being extruded at the proper locations. Since the
                syringe we are using only holds 150 ml of batter, we used positional
                control to ensure that once the syringe has been supressed 150 ml,
                the motor will stop. We also used a constant feed rate for our 
                extrusion motor.

'''

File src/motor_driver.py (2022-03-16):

'''!
@file       motor_driver.py
@brief      Driver class for the DC motors
@details    This file contains methods that will be
            utilized by the DC motors for the
            entirety of the quarter.
@author     Cesar Santana
@author     Jakob Frabosilio
@author     Ayden Carbaugh
'''
import pyb

class MotorDriver:
    '''!
    This class impliments a motor driver for an ME 405 kit.
    '''
    def __init__(self, en_pin, in1pin, in2pin, timer):
        '''!
        Creates a motor driver by initializing GPIO
        pins and turning the motor off for safety.
        @param en_pin poin used to enable the motor
        @param in1pin pin used to send PWM signal to motor
        @param in2pin pin used to send PWM signal to motor
        @param timer timer associated with the motor
        '''
        
        ## Cofigures the en_pin for the motor
        self.en_pin = en_pin
        ## Configures the in1pin for the motor
        self.in1pin = in1pin
        ## Configures the in2pin for the motor
        self.in2pin = in2pin
        ## Configures a timer for the motor
        self.timer = timer
        ## Configures cghannel 1 to the motor timer
        self.ch1 = self.timer.channel(1, pyb.Timer.PWM, pin=self.in1pin)
        ## Configures channel 2 to the motor timer
        self.ch2 = self.timer.channel(2, pyb.Timer.PWM, pin=self.in2pin)
      
    def set_duty_cycle(self, level):
        '''!
        This method sets the duty cycle to be sent
        to the motor to the given level. Posotive values
        cause torque in one direction, negative values
        in the opposite direction.
        @param level A signed intiger holding the duty
               cycle of the voltage sent to the motor
        '''
        self.en_pin.high()
        self.in1pin.low() 
        self.in2pin.low() 

        if level > 100:
            self.ch1.pulse_width_percent(100)
            self.ch2.pulse_width_percent(0)  
        elif level < -100:
            self.ch1.pulse_width_percent(0)
            self.ch2.pulse_width_percent(100)
        elif level>0:
            self.ch1.pulse_width_percent(abs(level))
            self.ch2.pulse_width_percent(0)
        elif level<0:
            self.ch1.pulse_width_percent(0)
            self.ch2.pulse_width_percent(abs(level))

class MotorDriverExtrude:
    '''!
    This class impliments a motor driver for an ME 405 kit.
    '''
    def __init__(self, pwmPin, timer, channel, directionPin):
        '''!
        Creates a motor driver by initializing GPIO
        pins and turning the motor off for safety.
        @param en_pin p 
        '''
        ## Configures the in1pin for the motor
        self.pwmPin = pwmPin
        ## Configures a timer for the motor
        self.timer = timer
        self.channel = channel
        self.dirPin = directionPin
        ## Configures cghannel 1 to the motor timer
        self.ch = self.timer.channel(self.channel, pyb.Timer.PWM, pin=self.pwmPin)
      
    def set_duty_cycle(self, level):
        '''!
        This method sets the duty cycle to be sent
        to the motor to the given level. Posotive values
        cause torque in one direction, negative values
        in the opposite direction.
        @param level A signed intiger holding the duty
               cycle of the voltage sent to the motor
        '''
        if level > 100:
            self.ch.pulse_width_percent(100)
            self.dirPin.high()
        elif level < -100:
            self.ch.pulse_width_percent(100)
            self.dirPin.low()
        elif level>0:
            self.ch.pulse_width_percent(abs(level))
            self.dirPin.high()
        elif level<0:
            self.ch.pulse_width_percent(abs(level))
            self.dirPin.low()
            
if __name__ == '__main__':
    pinC1 = pyb.Pin(pyb.Pin.board.PC1, pyb.Pin.OUT_PP)
    pinA0 = pyb.Pin(pyb.Pin.board.PA0, pyb.Pin.OUT_PP)
    pinA1 = pyb.Pin(pyb.Pin.board.PA1, pyb.Pin.OUT_PP)
    pinA10 = pyb.Pin(pyb.Pin.board.PA10, pyb.Pin.OUT_PP)
    pinB4 = pyb.Pin(pyb.Pin.board.PB4, pyb.Pin.OUT_PP)
    pinB5 = pyb.Pin(pyb.Pin.board.PB5, pyb.Pin.OUT_PP)
    pinB10 = pyb.Pin(pyb.Pin.board.PA9, pyb.Pin.OUT_PP)
    pinA7 = pyb.Pin(pyb.Pin.board.PA7, pyb.Pin.OUT_PP)
    trans_moe = MotorDriver(pinC1, pinA0, pinA1, pyb.Timer(5, freq = 20000))
    rad_moe = MotorDriver(pinA10, pinB4, pinB5, pyb.Timer(3, freq = 20000))
    ext_moe = MotorDriverExtrude(pinB10, pyb.Timer(1, freq = 20000), 2, pinA7)
    while True:
        rad_moe.set_duty_cycle(40)
    

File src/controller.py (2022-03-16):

'''!
@file          controller.py
@brief         Class for creating a proportional controller
@details       Class that initializes a proportional closed-loop controller.
               Contains methods to update actuation value
@author        Cesar Santana
@author        Jacob Frabosilio
@author        Ayden Carbaugh
'''

class PID:
    '''!
    This class utilizez PID control to generate outputs for a system
    '''
    
    def __init__(self, K_P, K_I, K_D, setpoint):
        '''!
        This creates a controller object
        @param K_P Proportional controller gain
        @param K_I Integral controller gain
        @param K_D Derivative controller gain
        @param setpoint Sets controller refernece value
        '''
        ## Reference Value for controller
        self.setpoint = setpoint
        #Proportional controller gain
        self.K_P = K_P
        ## Integral controller gain
        self.K_I = K_I
        ## Derivative controller gain
        self.K_D = K_D
        ## Desired time step to be used by the controller
        self.t_step = 0
        ## Error of the controller
        self.error = 0
        ## Proportional error of the controller
        self.P_error = 0
        ## Integral error of the controller
        self.I_error = 0
        ## Derivative error of the controller
        self.D_error = 0
        
        ## Stored time values
        self.time_vals = []
        ## Stored measured values
        self.meas_vals = []
        ## Stored reference values
        self.ref_vals = []
        
        ## Output value generated by the controller
        self.output = 0
    
    def ref(self, setpoint):
        '''!
        This method sets the target value for
        the controller
        @param setpoint Desired value for the controller 
        '''
        # Controller refernece value
        self.setpoint = setpoint
        
        # return self.setpoint
    
    def prop_gain(self, K_P):
        '''!
        This method sets the proportional gain for
        the controller
        @param K_P Proportional gain of the controller
        '''
        ## Proportional controller gain
        self.K_P = K_P
        
        return self.K_P
    
    def int_gain(self, K_I):
        '''!
        This method sets the integral gain for
        the controller
        @param K_I Integral gain of the controller
        '''
        
        ## Integral controller gain
        self.K_I = K_I
        
        return self.K_I
    
    def deriv_gain(self, K_D):
        '''!
        This method sets the derivative gain for
        the controller
        @param K_D Derivative gain of the controller
        '''
        ## Derivative controller gain
        self.K_D = K_D
        
        return self.K_D
    
    def compute(self, meas, t_step, save_data = False):
        '''!
        This method computes the total output of the PID controller by
        using the proportional, integral, and derivative error
        @param meas   Measured value to be corrected
        @param t_step Desired time step value
        '''
        ## Measuered value
        self.meas = meas
        ## Time step between measured values
        self.t_step = t_step
        
        if save_data:
            self.time_vals.append(t_step)
            self.meas_vals.append(meas)
            self.ref_vals.append(self.setpoint)
            
        self.error = self.setpoint - self.meas
        
        self.P_error = self.error
        
        self.I_error = self.error * self.t_step
         
        self.D_error = self.error / self.t_step
        
        self.output = self.P_error*self.K_P + self.I_error*self.K_I + self.D_error*self.K_D
        
        # if self.output > 100:
        #     self.output = 100
        # elif self.output < -100:
        #     self.output = -100
                
        return self.output
    
    def clear(self):
        '''!
        This method clears the lists containing time, measured,
        and refernece values
        '''
        
        self.time_vals = []
        
        self.meas_vals = []
        
        self.ref_vals = []

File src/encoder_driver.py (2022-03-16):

'''!
@file       encoder_driver.py
@brief      Driver class for quadrature encoders
@details    This file contains methods that will be
            utilized by the encoders throughout the
            entirety of the quarter.
@author     Cesar Santana
@author     Jacob Frabosilio
@author     Ayden Carbaugh
'''

import pyb

class EncoderDriver:
    '''!
    This class impliments an encoder driver for an ME 405 kit.
    '''
    
    def __init__(self, pin1, pin2, timer, CPR):
        '''!
        Creates an encoder driver by initializing pins on
        the shoe and configureing channels.
        @param pin1 pin associated with encoder channel A
        @param pin2 pin associated with encioder channel B
        @param timer timer associated with the encoder
        @param CPR number of encoder counts per revolution
        '''
        ## Position of the encoder
        self.pos = 0
        ## Change in position of the encoder
        self.delta = 0
        ## Starting time of the encoder
        self.start = 0
        ## Stopping time of the encoder
        self.stop = 0
        ## Configures pin1 for the encoder
        self.pin1 = pin1
        ## Configures pin 2 for the encoder
        self.pin2 = pin2
        ## Configures a timer for the encoder
        self.timer = timer
        
        ## Sets CPR value
        self.CPR = CPR
        
        ## Configures channel 1 to the encoder timer
        self.ch1 = self.timer.channel(1, pyb.Timer.ENC_A, pin=self.pin1)
        ## Configures channel 2 to the encoder timer
        self.ch2 = self.timer.channel(2, pyb.Timer.ENC_B, pin=self.pin2)
    
    def read(self):
        '''!
        This method calculates the position of the encoder
        and accounts for overflow.
        '''
        self.stop = abs(self.timer.counter())
        
        self.delta = self.stop - self.start
        
        if self.delta < -32768:
            
            self.delta = self.delta + 65536
            
        elif self.delta > 32768:
            self.delta = self.delta - 65536
        
        self.delta = self.delta * 360 / self.CPR
        self.pos += self.delta
        self.start = self.stop
        
        return self.pos
        
    def setpos(self, pos):
        '''!
        This methods sets the encoder position to a 
        user inputed value
        @param pos Desired encoder position
        '''
        self.pos = pos
        self.start = abs(self.timer.counter())
        
    def zero(self):
        '''!
        This methods resets the position of the encoder to zero.
        '''
        self.start = abs(self.timer.counter())
        self.pos = 0
        return self.pos

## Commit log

2022-02-15 solid models
    [Griddle.SLDPRT, Motor.SLDPRT, MotorAndEncoder.SLDPRT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]
2022-02-16 uploaded images and gif
    [14L1W8020.SLDPRT, Motor.SLDPRT, MotorAndEncoder.SLDPRT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]
2022-03-01 more CAD!
    [14L1W8020shorter.SLDPRT, Plunger.SLDPRT, PrelimAssembly.SLDASM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]
2022-03-01 more more CAD
2022-03-02 even more CAD
    [PrelimAssembly.SLDASM, SlideRail.SLDPRT, radialGearAssem.SLDASM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]
2022-03-02 part 1 of hardware design docs!
    [PrelimAssembly.SLDASM, SlideRail.SLDPRT]
2022-03-08 final solidworks!
    [14L1W8020shorter.SLDPRT, Part13^radialGearAssem.STL, Part14^radialGearAssem.STL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]
